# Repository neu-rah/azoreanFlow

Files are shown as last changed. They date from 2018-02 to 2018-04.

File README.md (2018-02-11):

# AzoreanFlow is a Hot Plate Reflow Soldering 
## Project  
Hardware by Christophe Persoz on 19/01/2018  
Software by Rui Azevedo  
Licence GNU General Public License v3

## WARNING and DISCLAIMER 
This project operates with possibly lethal AC voltage. If you are unsure what to do, don't do it and get help from an experienced tinkerer with professional training and skills.  

## TODO

* Alarms
* Choosing existing profiles
* Edit profiles
* Select time or temp drive (guess i will kill temp. drive, testing)
* Machine calibration
* Ensure profile fits the machine (after callibration)
* Store profiles

## Info
#### This is an Arduino-based reflow plate controller with
* PID loop control  
* Wave Packet and Phase Fired control for AC outputs  
* Use Zero Crossing SSR
* Graphic TFT LC-Display, drawing the temperature curves using a 1.8" TFT or derivate display
* Controlled using a ~~cheap rotary encoder and its~~ single button  
* ~~Stores up to 30 temperature profiles in EEPROM~~  (not yet)
* Configurable PID-parameters (only in code)
* Simple, small hardware to drive loads up to 400V and up to 6A  
* Hardware can measure two temperatures independently drive one AC load and one DC load, such as a fan

## Main Characteristics
* 2 K-thermocouple input associated to MAX31588 HE SPI controller  
* 2 SSR output (One for Heat Plate - 6A, the other for a 12V Fan - 1A)  
* ~~Rotary encoder with switch for user input~~
* TFT 1.8" HW SPI Color display for feedback and control  
* Beeper for advertising  

~~Please Note: Requires Arduino IDE 1.5.x or newer.~~
Based on 0xPIT hardware, but contains a lot of updates on hardware and a complete new software.

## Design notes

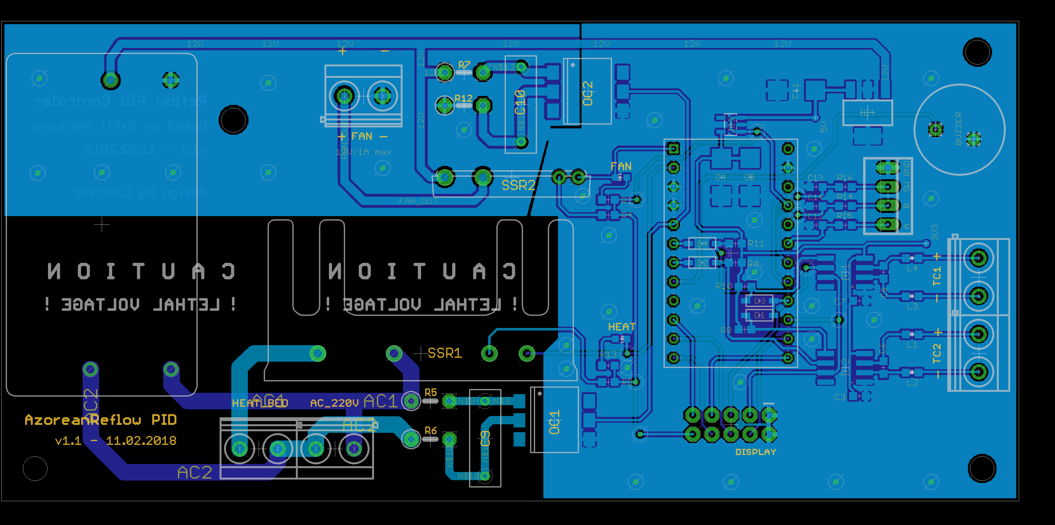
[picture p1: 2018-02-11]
hardware/Azorean Reflow v1.1 Board Preview.png

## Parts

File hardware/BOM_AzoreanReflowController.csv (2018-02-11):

Qty | Value | Device | MOUSER_REF | Parts | Package | Description
1 |  | FAN 120x120mm | CFM-A225-13-10 | FAN |  | Ventilateurs CC Ventilateurs CC DCFan 126.89CFM9.48W 12V 120x120x25.4mmAR
1 |  | 1,6/0,8 | 254-EMB140-RO | BUZZER PAD1 | 1,6/0,8 | THROUGH-HOLE PAD
1 |  | 1,6/0,8 | 254-EMB140-RO | BUZZER PAD2 | 1,6/0,8 | THROUGH-HOLE PAD
4 |  | DIODESOD-123 | 1N4148W-7-F | D1, D2, D3, D4 | SOD-123 | Diode
4 |  | INDUCTOR0603 | BLM18PG471SN1D | L1, L2, L3, L4 | L0603 | Inductors
1 |  | M05X2SHD-NS |  | DISPLAY | 2X5-SHROUDED-NS | Header 5x2
2 | 0.1uF | 0.1UF-0603-25V-5% | VJ0603Y104JXJPW1BC | C3, C7 | L0603 | 0.1µF ceramic capacitors
1 | 100R | R-EU_0207/5V | 273-100-RC | R1 | 0207/5V | RESISTOR, European symbol
2 | 100n | C-EU025-025X050 | R71VF3100AA30K | C9, C10 | C025-025X050 | CAPACITOR, European symbol
1 | 100n | CXXC10B5 | R46KF310000M1M | C1 | XC10B5 | X CAPACITOR
4 | 10k | R-EU_R0603 | WCR0603-10KFA | R8, R9, R10, R11 | R0603 | RESISTOR, European symbol
1 | 10n | C-EUC0603 | C0603C103K4RACTM | C6 | C0603 | CAPACITOR, European symbol
1 | 10n | C-EUC0603 | C0603C103K4RACTM | C8 | C0603 | CAPACITOR, European symbol
3 | 10µ | CPOL-EUC/6032-28R | T491C106K025AT7280 | C4, C5, C11 | C/6032-28R | POLARIZED CAPACITOR, European symbol
2 | 120R | R-EU_R0603 | RC0603FR-07120RL | R3, R4 | R0603 | RESISTOR, European symbol
2 | 3.3k | R-EU_R0603 | RC0603FR-073K3L | R2, R13 | R0603 | RESISTOR, European symbol
4 | 47k | R-EU_0207/5V | 273-47K-RC | R5, R6, R7, R12 | 0207/5V | RESISTOR, European symbol
1 | 4P-2.0 | GROVE-CONNECTOR-DIP(4P-2.0) |  | ENC | HW4-2.0 | 320110033
1 | AQZ205D | AQZ205D | AQZ205 | K3 | AQZ-SIL04 | PhotoMOS Relay NAiS
1 | ARDUINO_PRO_MICRO | ARDUINO_PRO_MICRO |  | A1 | ARDUINO_PRO_MICRO | SparkFun Pro Micro 5V/16MHz
1 | FAN | LEDCHIP-LED0603 | APA3010QBC/D-GX | LD2 | CHIP-LED0603 | LED
2 | H11A1SM | H11A1SM | H11AA1-X009T | OC1, OC2 | DIL6-SMD | General Purpose 6-Pin Phototransistor Optocouplers
1 | HEAT | LEDCHIP-LED0603 | APA3010QBC/D-GX | LD1 | CHIP-LED0603 | LED
1 | IRM-10-12 | IRM-10-12 | IRM-10-12 | PWR-MOD | IRM-10-12 | Power Supply IRM-10-12
1 | LP298XS | LP298XS | LP2985-33DBVR | IC3 | SOT23-5L
2 | MAX31855 | MAX31855 | MAX31855KASA+ | IC1, IC2 | SOIC8
1 | MIC5201-5 | MIC5201-5 | MIC2920A-5.0WS | IC4 | SOT-223 | Micrel MIC5201 200mA Low-Dropout Regulator
5 | MKDSN1,5/2-5,08 | MKDSN1,5/2-5,08 | 1715721 | AC_220V, FAN, HEAT_BED, TC1, TC2 | MKDSN1,5/2-5,08 | MKDSN 1,5/ 2-5,08 Printklemme
1 | PF240D25 | PF240D25 | PF240D25 | K1 | PF240XX | PF Series
2 | TPTP08R | TPTP08R |  | 3V3, 5V | TP08R | Test pad

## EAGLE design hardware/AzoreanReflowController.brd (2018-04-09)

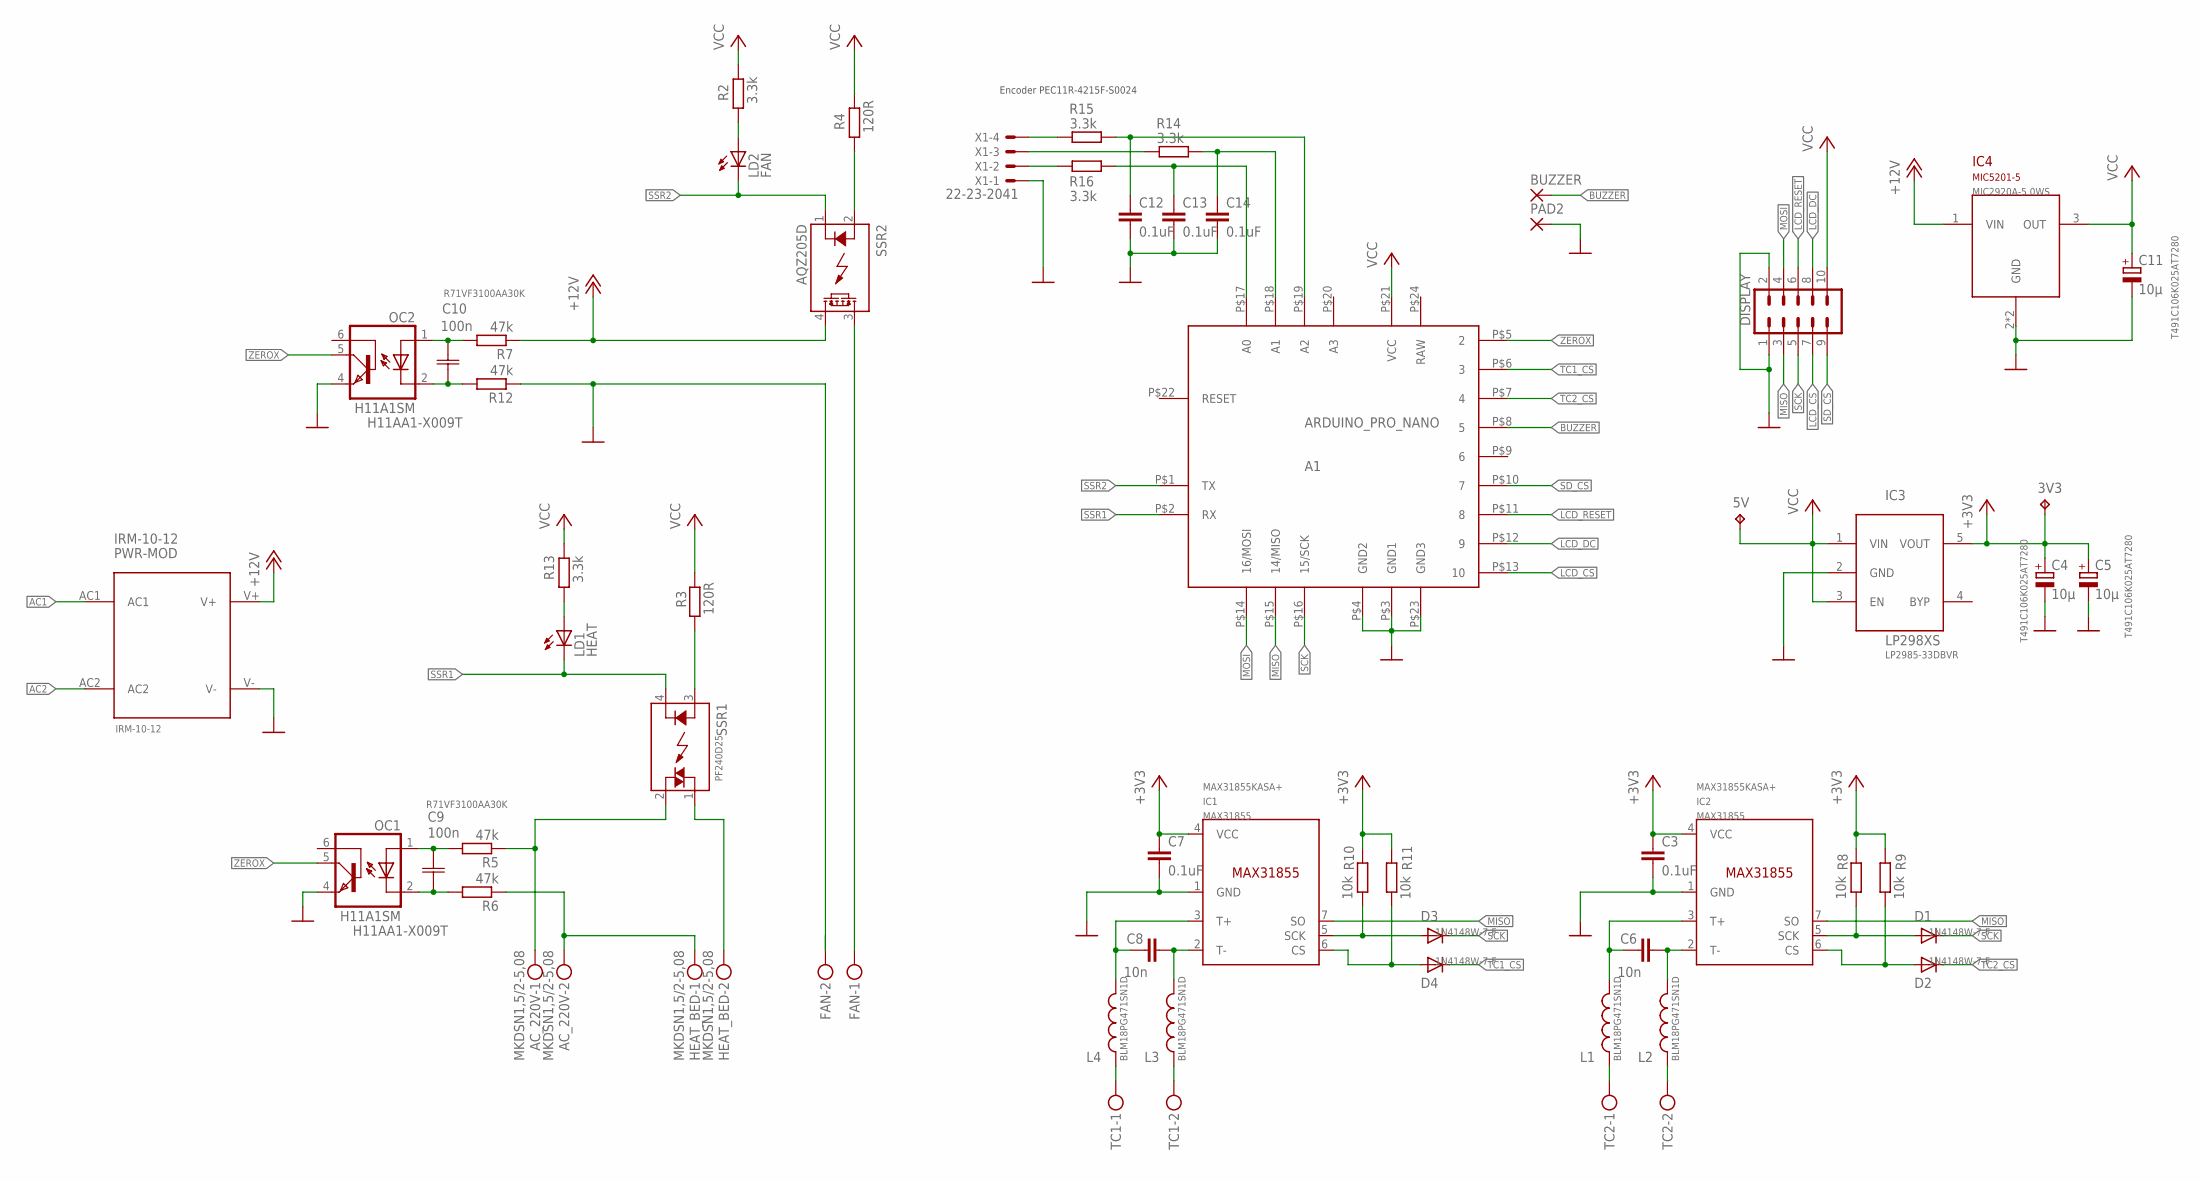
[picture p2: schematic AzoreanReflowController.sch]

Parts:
3V3, 5V: TPTP08R; TP08R
A1: ARDUINO_PRO_NANO
AC_220V: MKDSN1,5/2-5,08
BUZZER: 1,6/0,8
C3, C7, C12, C13, C14: 0.1uF; 0603
C4, C5, C11: 10µ; C/6032-28R
C6, C8: 10n; C0603
C9, C10: 100n; R71V
D1, D2, D3, D4: DIODESOD-123; SOD-123
DISPLAY: M05X2SHD-NS; 2X5-SHROUDED-NS
FAN: MKDSN1,5/2-5,08
HEAT_BED: MKDSN1,5/2-5,08
IC1, IC2: MAX31855; SOIC8
IC3: LP298XS; SOT23-5L
IC4: MIC5201-5; SOT-223
L1, L2, L3, L4: INDUCTOR0603; 0603
LD1: HEAT; CHIP-LED0603
LD2: FAN; CHIP-LED0603
OC1, OC2: H11A1SM; DIL6-SMD
PAD2: 1,6/0,8
PWR-MOD: IRM-10-12
R2, R13, R14, R15, R16: 3.3k; R0603
R3, R4: 120R; R0603
R5, R6, R7, R12: 47k; 0207/5V
R8, R9, R10, R11: 10k; R0603
SSR1: PF240D25; PF240XX
SSR2: AQZ205D; AQZ-SIL04
TC1, TC2: MKDSN1,5/2-5,08
X1: 22-23-2041

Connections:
12V: IC4.1 (VIN), PWR-MOD.V+, R7.1, SSR2.4 (DS2)
+3V3: 3V3.TP, C3.1, C4.+, C5.+, C7.1, IC1.4 (VCC), IC2.4 (VCC), IC3.5 (VOUT), R8.2, R9.2, R10.2, R11.2
AC1: AC_220V.1, PWR-MOD.AC1, R5.1, SSR1.2 (ACL2)
AC2: AC_220V.2, HEAT_BED.1, PWR-MOD.AC2, R6.1
AC_OUT1: HEAT_BED.2, SSR1.1 (ACL1)
BUZZER: A1.P$8 (5), BUZZER.1
FAN_OUT: FAN.1, SSR2.3 (DS1)
GND: A1.P$3 (GND1), A1.P$4 (GND2), A1.P$23 (GND3), C3.2, C4.-, C5.-, C7.2, C11.-, C12.2, C13.2, C14.2, DISPLAY.1, DISPLAY.2, FAN.2, IC1.1 (GND), IC2.1 (GND), IC3.2 (GND), IC4.2 (GND), IC4.4 (GND), OC1.4 (EMI), OC2.4 (EMI), PAD2.1, PWR-MOD.V-, R12.1, X1.1
LCD_CS: A1.P$13 (10), DISPLAY.7
LCD_DC: A1.P$12 (9), DISPLAY.8
LCD_RESET: A1.P$11 (8), DISPLAY.6
MISO: A1.P$15 (14/MISO), DISPLAY.3, IC1.7 (SO), IC2.7 (SO)
MOSI: A1.P$14 (16/MOSI), DISPLAY.4
unnamed: C8.2, IC1.2 (T-), L3.2
unnamed: C6.2, IC2.2 (T-), L2.2
unnamed: C6.1, IC2.3 (T+), L1.2
unnamed: A1.P$17 (A0), C13.1, R16.2
unnamed: A1.P$18 (A1), C14.1, R14.2
unnamed: L1.1, TC2.1
unnamed: A1.P$19 (A2), C12.1, R15.2
unnamed: C9.1, OC1.1 (A), R5.2
unnamed: C9.2, OC1.2 (C), R6.2
unnamed: C8.1, IC1.3 (T+), L4.2
unnamed: C10.1, OC2.1 (A), R7.2
unnamed: R3.2, SSR1.3 (DC+)
unnamed: R4.2, SSR2.2 (A)
unnamed: D2.A, IC2.6 (CS), R9.1
unnamed: D1.A, IC2.5 (SCK), R8.1
unnamed: D4.A, IC1.6 (CS), R11.1
unnamed: D3.A, IC1.5 (SCK), R10.1
unnamed: C10.2, OC2.2 (C), R12.2
unnamed: R16.1, X1.2
unnamed: R14.1, X1.3
unnamed: L4.1, TC1.1
unnamed: L3.1, TC1.2
unnamed: L2.1, TC2.2
unnamed: LD2.A, R2.2
unnamed: R15.1, X1.4
unnamed: LD1.A, R13.2
RAW: A1.P$24 (RAW)
SCK: A1.P$16 (15/SCK), D1.C, D3.C, DISPLAY.5
SD_CS: A1.P$10 (7), DISPLAY.9
SSR1: A1.P$2 (RX), LD1.C, SSR1.4 (DC-)
SSR2: A1.P$1 (TX), LD2.C, SSR2.1 (K)
TC1_CS: A1.P$6 (3), D4.C
TC2_CS: A1.P$7 (4), D2.C
VCC: 5V.TP, A1.P$21 (VCC), C11.+, DISPLAY.10, IC3.1 (VIN), IC3.3 (EN), IC4.3 (OUT), R2.1, R3.1, R4.1, R13.1
ZEROX: A1.P$5 (2), OC1.5 (COL), OC2.5 (COL)

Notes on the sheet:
Encoder PEC11R-4215F-S0024

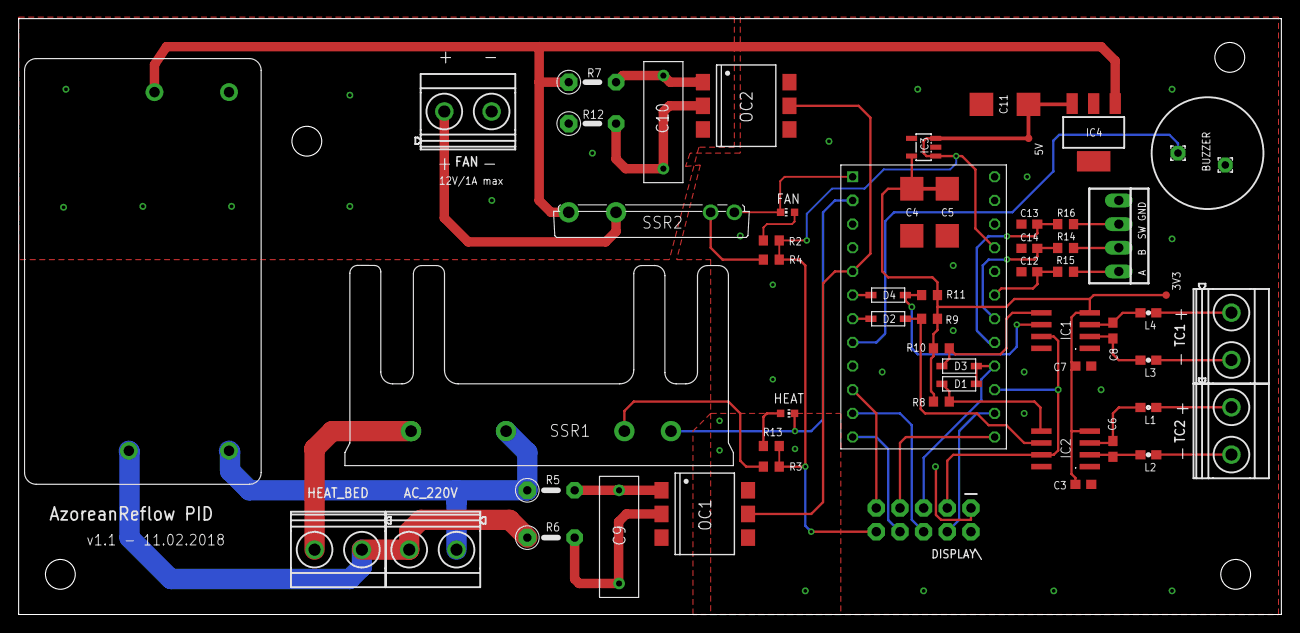
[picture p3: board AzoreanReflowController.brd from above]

Board: 2 copper layers, 135.6 x 64.0 mm, 58 parts (0 on the bottom side), 47 nets.

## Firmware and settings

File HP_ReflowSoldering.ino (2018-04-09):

/*******************************************************************************
 * Title: Hot Plate Reflow Controller
 * Version: 1.0.0
 * Date: 19-01-2018
 * Company: Christophe Persoz
 * Author: Christophe Persoz and Rui Avezado
 * Website: www.christophepersoz.com
 *
 * Brief
 * =====
 * This is an example firmware for our Arduino compatible reflow hot plate controller.
 * The reflow curve used in this firmware is meant for lead-free profile
 * (it's even easier for leaded process!). You'll need to use a special version of
 * the MAX31855 library for Arduino which can be downloaded from my GitHub repository.
 * Please check our wikI for more information on using this piece of code
 * together with the hot plate reflow controller shield.
 *
 * Disclaimer
 * ==========
 * Dealing with high voltage is a very dangerous act! Please make sure you know
 * what you are dealing with and have proper knowledge before hand. Your use of
 * any information or materials on this reflow oven controller is entirely at
 * your own risk, for which we shall not be liable.
 *
 * Licences
 * ========
 * This reflow oven controller hardware and firmware are released under the
 * Creative Commons Share Alike v3.0 license
 * http://creativecommons.org/licenses/by-sa/3.0/
 * You are free to take this piece of code, use it and modify it.
 * All we ask is attribution including the supporting libraries used in this
 * firmware.
 *
 * Required Libraries
 * ==================
 * - Arduino PID Library:
 *   >> https://github.com/br3ttb/Arduino-PID-Library
 *
 * Revision  Description
 * ========  ===========

 1.00		Initial release.

 *******************************************************************************/
// Board using MAX31855KASA+ chip

#include <TimerOne.h>
#include "src/azorean.h"

void timerIsr() {_ENC.service();}

void setup()
{
#ifdef DEBUG
    Serial.begin(115200);
    while (!Serial) {}
#endif
    
    // SSR pin initialization to ensure reflow plate is off
    pinMode(HP_SSR, OUTPUT);
    digitalWrite(HP_SSR, HP_OFF);
    pinMode(FAN_SSR, OUTPUT);
    digitalWrite(FAN_SSR, FAN_OFF);

    //clickEncoder timer
    Timer1.initialize(1000);
    Timer1.attachInterrupt(timerIsr);
    _ENC.setAccelerationEnabled(false);
    _ENC.setDoubleClickEnabled(true);

    // Buzzer pin initialization to ensure annoying buzzer is off
    pinMode(BEEPER, OUTPUT);
    digitalWrite(BEEPER, LOW);

    // Zero Crossing
    // pinMode(ZERO_X, INPUT_PULLUP);

    // Start-up splash + beep
    _TFT.begin(UCG_FONT_MODE_SOLID);
    #ifdef Neurs
        _TFT.setRotate90();
    #else
        _TFT.setRotate270();
    #endif

    // Thermocouple
    _THRM1.setVerbose(TH_Verb);
    _THRM2.setVerbose(TH_Verb);

    // Shortly turn on SSR
    digitalWrite(HP_SSR, HP_ON);
    digitalWrite(FAN_SSR, FAN_ON);
    tone(BEEPER,BEEP_FREQ,400);

    // Turn off SSR
    digitalWrite(HP_SSR, HP_OFF);
    digitalWrite(FAN_SSR, FAN_OFF);

    splash();
#ifdef DEBUG
    Serial<<"Click to start reflow..."<<endl;
#endif
}

//do a reflow cycle
void loop(){
    switch(_ENC.getButton()) {
        case ClickEncoder::Clicked:
            run=true;
            reflow();
#ifdef DEBUG
            Serial<<"Click to continue..."<<endl;
#endif
            while(_ENC.getButton()!=ClickEncoder::Clicked);//wait for click at end
            splash();
            break;
        case ClickEncoder::DoubleClicked://editing?
            digitalWrite(FAN_SSR,!digitalRead(FAN_SSR));
        default:break;
    }
}

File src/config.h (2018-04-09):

/* -*- C++ -*- */
// ***** INCLUDES *****
#ifndef HP_REFLOW_CONFIG_H
#define HP_REFLOW_CONFIG_H

  //#ifdef DEBUG
    #include <streamFlow.h>
  //#endif
  #include <HP_MAX31855.h>			// Thermocouple HW SPI
  #include <PID_v1.h>				// PID library
  #include <ClickEncoder.h>			// Rotary encoder + switch
  #include <Ucglib.h>				// HW SPI TFT Graphic display
  // #include "flow.h"

  // ***** CONSTANTS *****
    #define VERSION "1.01"
    #define NAME    "azoreanREFLOW"

  #define FAN_ON LOW
  #define FAN_OFF HIGH
  #define HP_ON LOW
  #define HP_OFF HIGH

  #define TEMPERATURE_ROOM 33
  //#define TEMP_COMPENSATION 0

  constexpr unsigned long PID_SAMPLE_TIME=1000;
  constexpr unsigned long COMPENSATION=PID_SAMPLE_TIME;

  enum DriveMode {TempDrived,TimeDrived};
  constexpr DriveMode driveMode=TimeDrived;

  #define PID_KP				300 //1.75 // 300
  #define PID_KI				0.05 //0.03 // 0.05
  #define PID_KD				250 //3.0  // 250

  #define tempColor             174,255,0
  #define baseColor             235,235,235
  #define auxColor              63,63,63
  #define hiliteColor           255,161,0
  #define selColor              tempColor

  #ifdef Neurs
    // ***** PIN ASSIGNMENT in Azores ;) *****
    constexpr uint8_t HP_SSR  = 17;//5;	// Pin for SSR1
    constexpr uint8_t FAN_SSR = 19;	// Pin for SSR2

    constexpr uint8_t TH1_CS  = A6;	// Pin for Thermocouple 1
    constexpr uint8_t TH2_CS  = A7;	// Pin for Thermocouple 2
    constexpr bool TH_Verb = false;

    constexpr uint8_t ZERO_X  = 18;	// Pin for zero crossing detector
    constexpr uint8_t BEEPER  = 6;	// Beeper

    constexpr uint8_t SW_ENC  = 4;	// Rotary Encoder Switch
    constexpr uint8_t A_ENC   = 2;	// Rotary Encoder A
    constexpr uint8_t B_ENC   = 3;	// Rotary Encoder B

    constexpr uint8_t ENC_STEPS_PER_NOTCH = 4; // Encoder Step Notch
    constexpr uint8_t TFT_CS   = A1;
    constexpr uint8_t TFT_DC   = A0;
    constexpr uint8_t TFT_RST  = A2;
  #else
    //this ignores fakeHW calls
    #define fakeHW(x)

    // ***** PIN ASSIGNMENT *****
    constexpr uint8_t HP_SSR  = 0;	// Pin for SSR1
    constexpr uint8_t FAN_SSR = 1;	// Pin for SSR2
    constexpr uint8_t TH1_CS  = 3;	// Pin for Thermocouple 1
    constexpr uint8_t TH2_CS  = 4;	// Pin for Thermocouple 2
    constexpr bool    TH_Verb = false;
    constexpr uint8_t ZERO_X  = 2;	// Pin for zero crossing detector
    constexpr uint8_t BEEPER  = 5;	// Beeper
    constexpr uint8_t SW_ENC  = A0;	// Rotary Encoder Switch
    constexpr uint8_t A_ENC   = A1;	// Rotary Encoder A
    constexpr uint8_t B_ENC   = A2;	// Rotary Encoder B
    constexpr uint8_t ENC_STEPS_PER_NOTCH = 4; // Encoder Step Notch
    constexpr uint8_t TFT_CS   = 10;
    constexpr uint8_t TFT_DC   = 9;
    constexpr uint8_t TFT_RST  = 8;

  #endif

  #if defined(DEBUG) && defined(TRACE)
    #define trace(x) x
  #else
    #define trace(x)
  #endif
  #ifdef DEBUG
    #define _trace(x) x
  #else
    #define _trace(x)
  #endif

#endif

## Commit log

2018-02-11 Add Hardware
    Add PCB, schematics and BOM for AzoreanFlow
    [AzoreanReflowController.brd, AzoreanReflowController.sch, BOM_AzoreanReflowController.csv]
2018-04-09 Update for DEBUG
    Now serial output is optional by activating #define DEBUG
    [AzoreanReflowController.brd]

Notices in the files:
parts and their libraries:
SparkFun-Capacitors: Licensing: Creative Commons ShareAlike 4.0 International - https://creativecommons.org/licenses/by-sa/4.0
